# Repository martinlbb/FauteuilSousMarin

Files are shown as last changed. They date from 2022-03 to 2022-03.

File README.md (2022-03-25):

# FauteuilSousMarin

## Le projet 

Projet de Fauteuil sousmarin pour [Odysseus 3.1](https://odysseus31.com/ "Odysseus 3.1"), association à Lyon.

L'idée est de répliquer les mouvements du fauteuil spatial de la NASA dans les années 1980 sous l'eau.

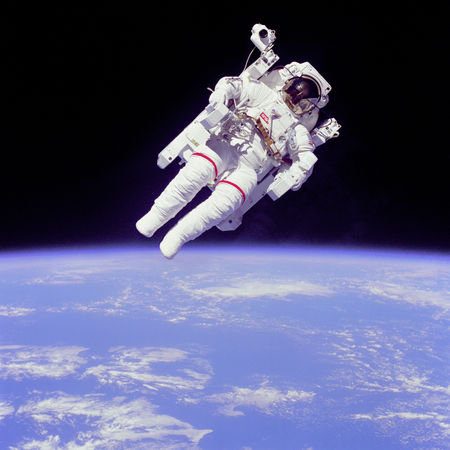
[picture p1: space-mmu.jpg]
<br><br>

Sous l'eau, pas de gravité, donc il est possible de simuler le fonctionnement d'un fauteuil spatial, pour se déplacer comme dans l'espace.

### Pour qui ?

* Pour les spationautes en formations (entrainement)
* Pour des personnes handicapées, qui seront prise en charge dans leurs déplacement sous l'eau.

## Principe du projet

Un fauteuil (cadre en tube soudé) acceuille le plongeur, son bloc d'air, deux joysticks, les moteurs et les batteries.

Le système est controllé par deux joysticks, inspirés directement des commandes de la NASA.
Une commande permet la translation du fauteuil sur les 3 axes (main gauche).
Une commande permet la rotation du fauteuil sur les 3 axes (main droite).
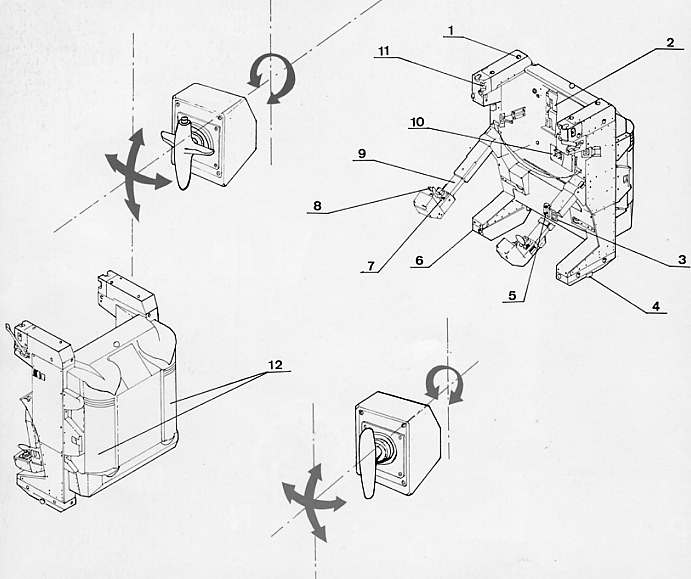
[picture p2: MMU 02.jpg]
<br><br>

Une commande à distance (Monitor box) permet le contrôle du fauteuil à distance, en parallèle ou en remplacement des commandes sur le fauteuil. Cette commande permet aussi d'armer le fauteuil lors de la mise à l'eau, pour éviter des salades de doigts (ou cheveux, ceinture de plomb, ...) avec les propulseurs.

Le fauteuil selon deux modes :
* plongée (normal) : quand l'ordre (joystick) s'arrête, l'action correspondante s'arrête
* espace (space) : quand l'ordre (joystick) s'arrête, l'action continue, comme dans l'espace. Le système est a améliorer, pour être plus réaliste. 

**DANGER**
Le surnom du mode 'espace' c'est 'Vicieux', vu les marches avant plein gaz (malgré l'arrêt de la commande) dans les murs de la piscine qui a servi aux tests. Bah oui, dans l'espace, quand tu as mis gaz avant toutes, il te faut gaz arrière toute pour compenser la première commande....

## Electronique

Un microcontrolleur Arduino gère le 'SpaceChair', en utilisant les entrées des joysticks et en dirigeant les propulseurs. Un mode 'SpaceMode' permet de simuler

Il contrôle ensuite 6 ESC (contrôlleur de moteur brushless (triphasé)) comme en modélisme.
Il y a 6 moteurs, 3 par axes et 2 par sens (avant/arrière). Je l'ai conçu pour équilibrer l'effet gyroscopique (moteur sens horaire et contra sens horaire sur chaque axe) et permettre plus de finesse.

## Impression 3D

De nombreux éléments du fauteuil ont été désignés sous openSCAD. Boitier de commande, protection des joysticks sous l'eau, chapeau des joysticks avec la réplique des commandes NASA.

## Annexes

### Le fauteuil MMU

Nasa: Manned Maneuvering Unit ou MMU, utilisé en 1984 !
Retiré car trop dangereux (24,4m/s de vitesse, donc en cas d'erreur, c'est bye bye la station et bonjour l'effet **vers l'infini et au delà**).
Depuis, passage au Simplified Aid for EVA Rescue : SAFER.
Il fait un delta de 3,3 m/s

MMU: 24 petites tuyères, chacune pouvant créer une poussée de 7,5 kg
3-axes Translatio controlleur (main gauche)
3-axes Rotation controlleur (main gauche)
Commandes simple ou mutli-axes en continues ou impulsions.

Son mode d'emploi : http://large.stanford.edu/courses/2014/ph240/clark1/docs/mcr-78-617.pdf

Un site qui en parle : http://capcomespace.net/dossiers/espace_US/shuttle/sts/EMU_MMU/MMU.htm

### Liste des composants
Voir aussi dans le dossier Datasheets !

* 6 moteurs, en 3 lots de CW et CWW https://www.aliexpress.com/item/32965239368.html
* 6 controlleurs 90A étanche : https://hobbyking.com/fr_fr/hobbyking-90a-boat-esc-4a-sbec.html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
* 1 télécommande de programmation : https://hobbyking.com/fr_fr/hobbyking-boat-esc-programming-card.html
* 4 joysticks 3 axes :  JH-D300X-R4 https://www.aliexpress.com/item/32992844960.html
* 6 potentiometres IP68 Vishay P13SM : https://www.vishay.com/docs/51064/p13sm.pdf
* 2 Arduino Micro

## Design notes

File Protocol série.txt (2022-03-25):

$G:

Start sequence=$
End sequence  =!

Commandes:
G pour commande joystick
	G:translateX%:translateY%:translateZ%:rotateX%:rotateY%:rotateZ%!
H pour commande joystick qui prends la main
	G:translateX%:translateY%:translateZ%:rotateX%:rotateY%:rotateZ%!
M pour Mode
	M:mode!
	parameters
		SPACE as S, SpaceMode
		DIVE as D,  DiveMode
		ARMED as A
		DISARMED as X
D pour Debug
	$D!
	S'inverse tout seul à chaque ordre
S pour Save
	$S!
	Sauve les paramètres dans l'eeprom interne
P pour parameter
	P:parametername:value:value!
	parameters
		INVERSE as I, Translate(T) or Rotate (R), which axis (X,Y or Z), inverse it(1) or not (0). $P:I:T:X:1!
		NEUTRAL as N, percentage value. $P:N:8!
		THRUSTER as T, Forward(F) or Reverse (R), which axis (X,Y or Z), max running %. $P:T:R:Z:70!
		KINETIC as K, percentage of ignored kinetc value. $P:K:10!

$P:I:T:Z:1!

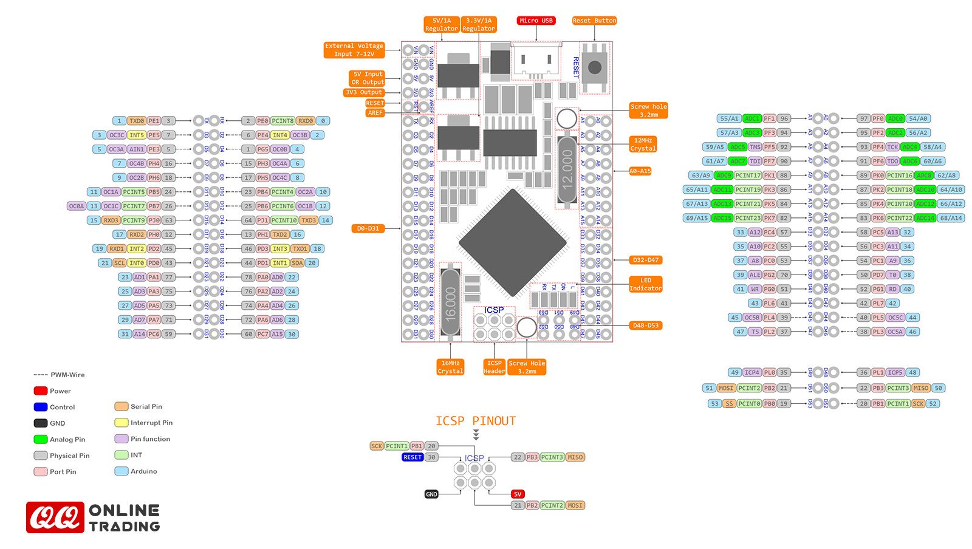
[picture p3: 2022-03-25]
datasheets/mega 2560 pro embed pinout.jpg

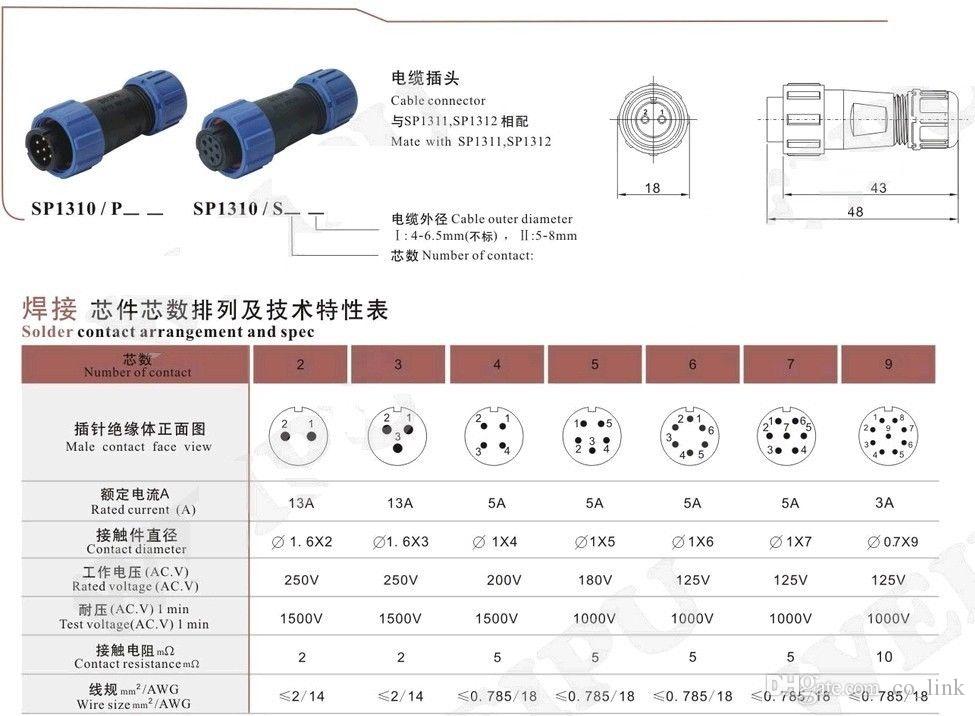
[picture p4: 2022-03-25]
datasheets/IP68-SP13-elec.jpg

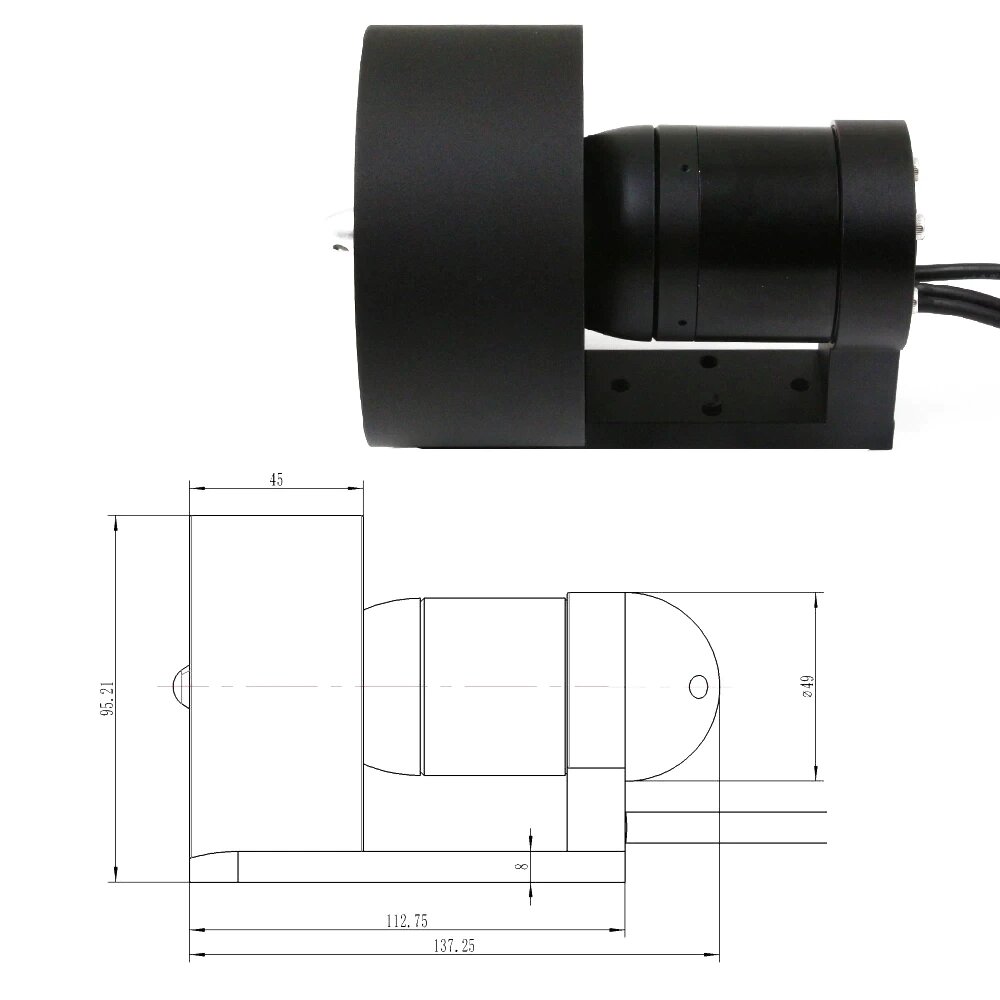
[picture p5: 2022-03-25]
datasheets/DS-02Thruster Profil.jpg

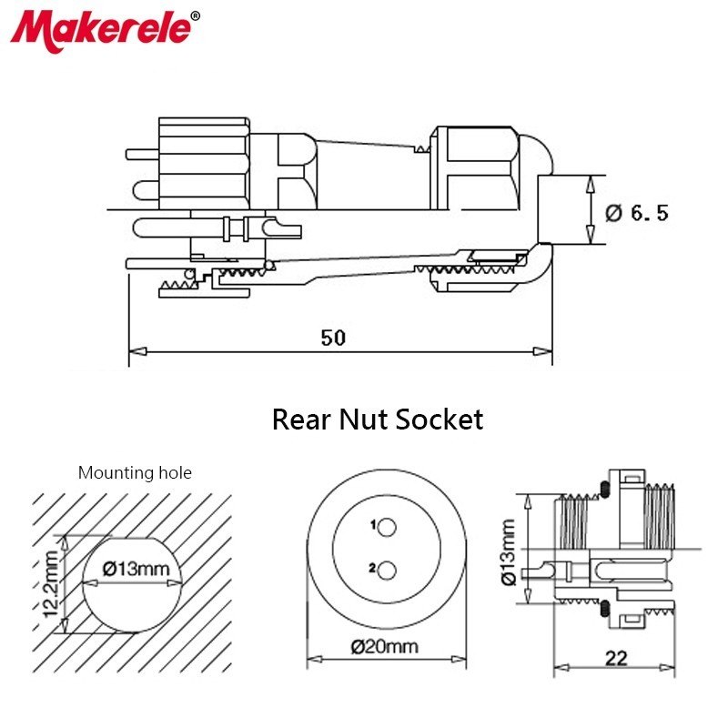
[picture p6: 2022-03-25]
datasheets/IP68-SP13.jpg

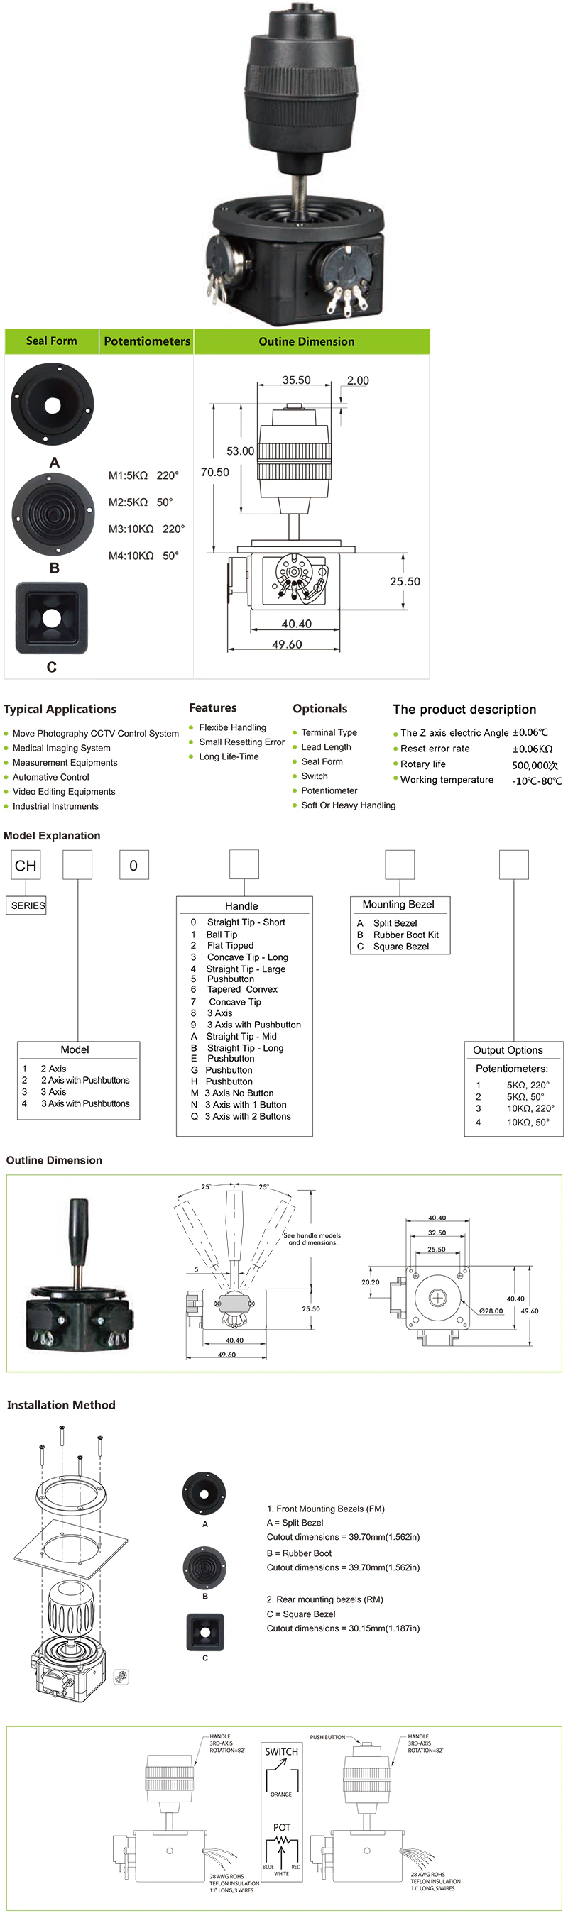
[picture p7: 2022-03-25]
datasheets/joystick-3axis.jpg

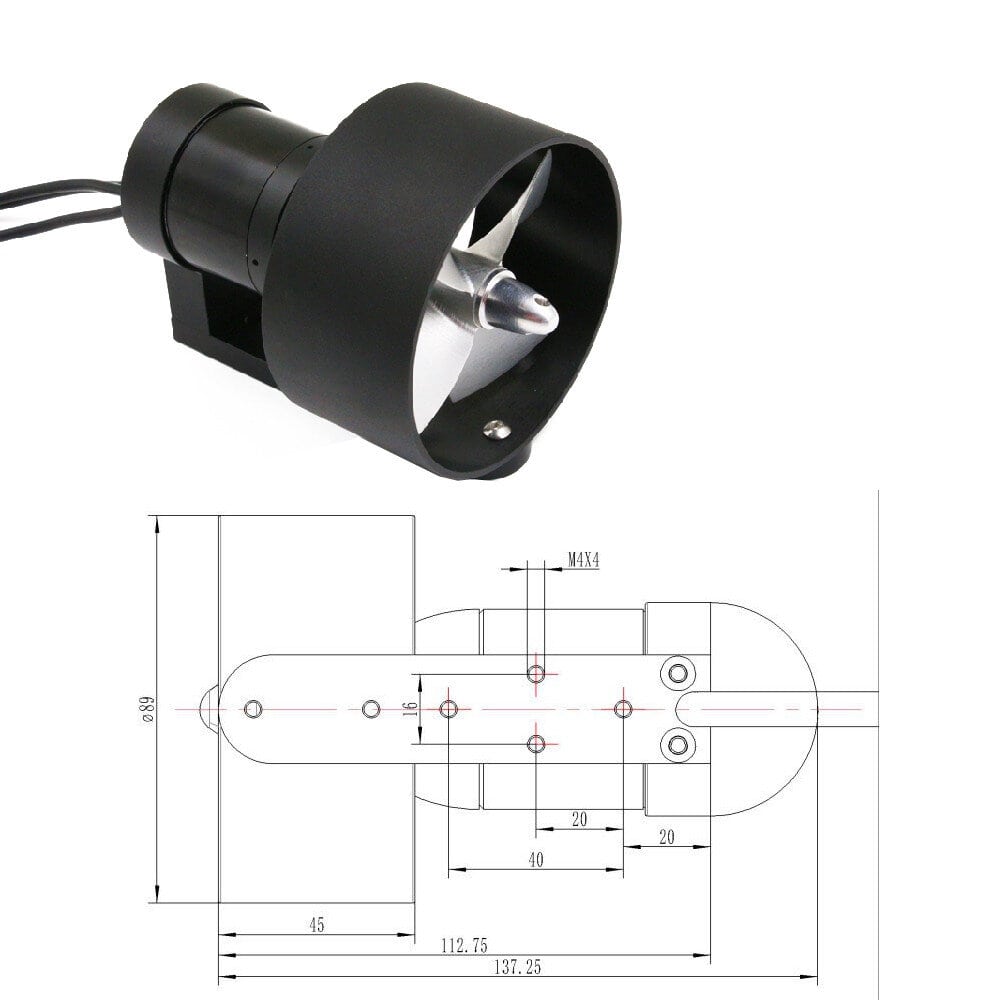
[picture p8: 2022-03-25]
datasheets/DS-02 Thruster fond_.jpg

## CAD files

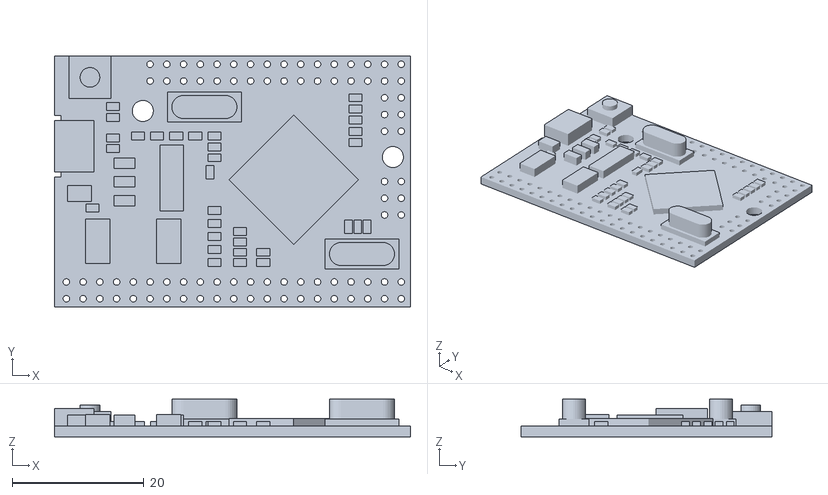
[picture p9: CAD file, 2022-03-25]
Monitor box/Box 3D/Mega_2560_PRO_Embed_CH340G.stl
54.0 x 38.0 x 5.70

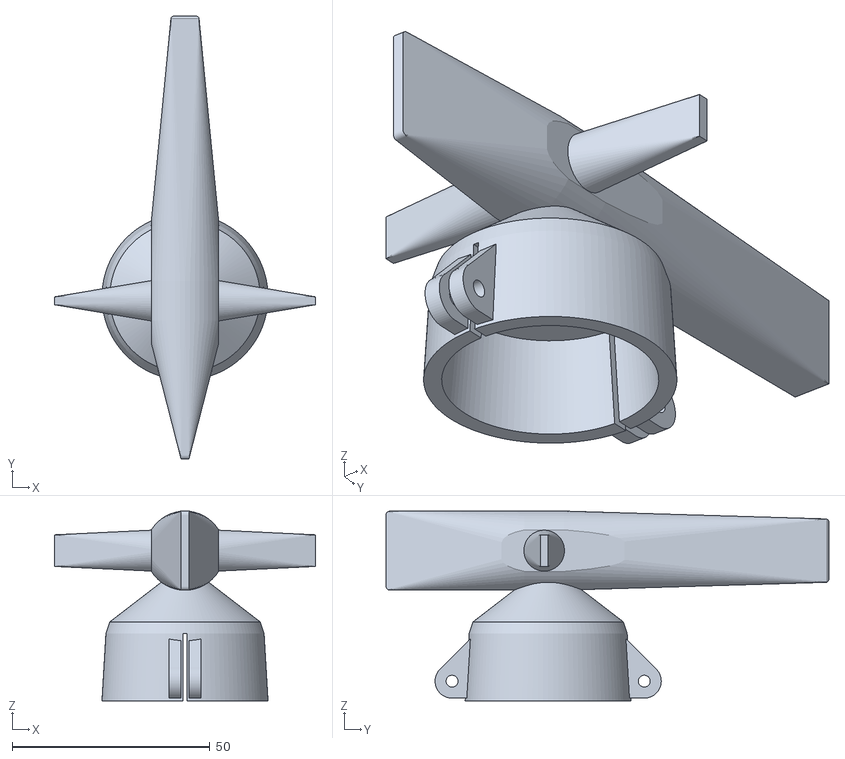
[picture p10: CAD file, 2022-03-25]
SpaceChair/joystick_rotate.stl
66.0 x 112.0 x 48.0

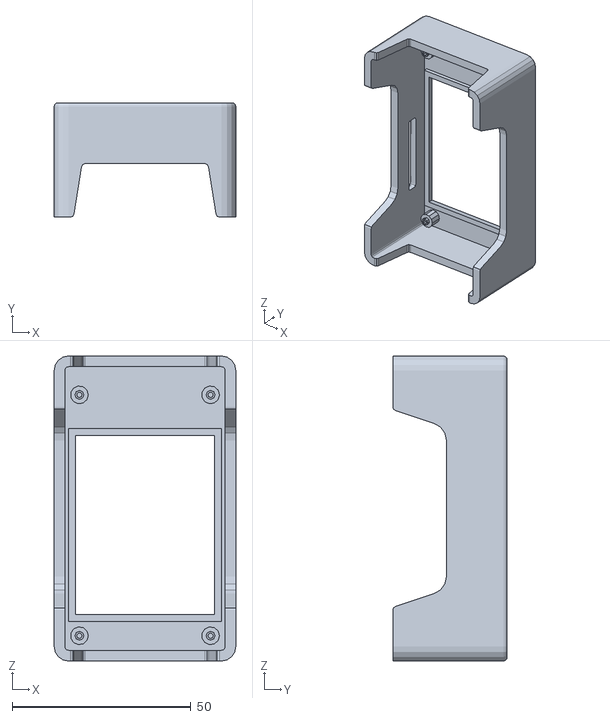
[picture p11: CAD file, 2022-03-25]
Monitor box/Box 3D/TFT_housing.stl
50.8 x 32.0 x 85.3

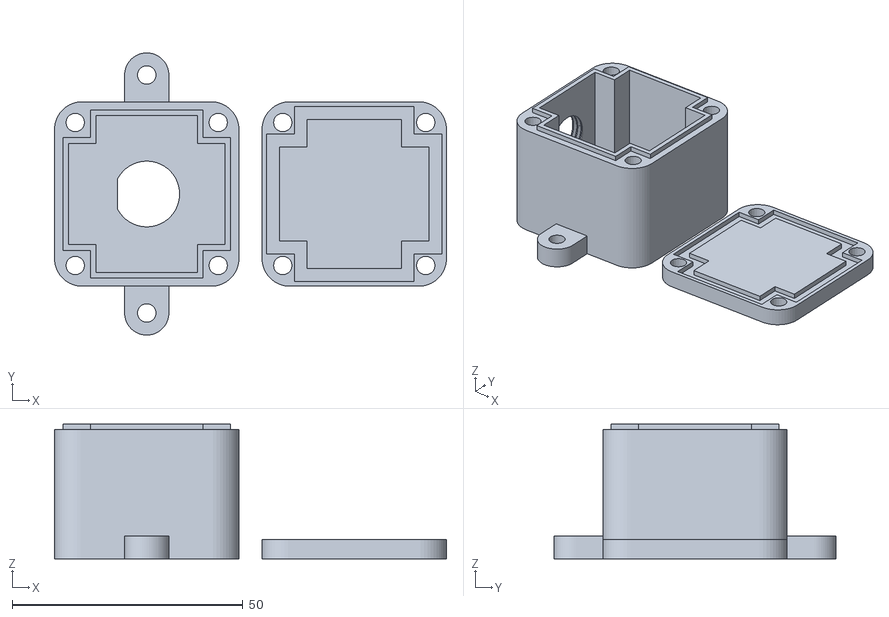
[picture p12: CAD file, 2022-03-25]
SpaceChair/box_surface_link.stl
85.0 x 61.2 x 29.2

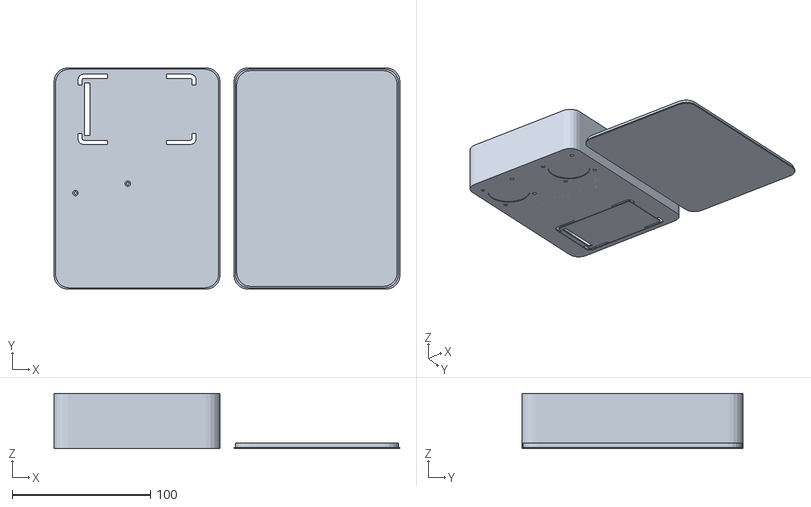
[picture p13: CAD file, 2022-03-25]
Monitor box/Box 3D/monitor_box.stl
250.0 x 160.0 x 40.0

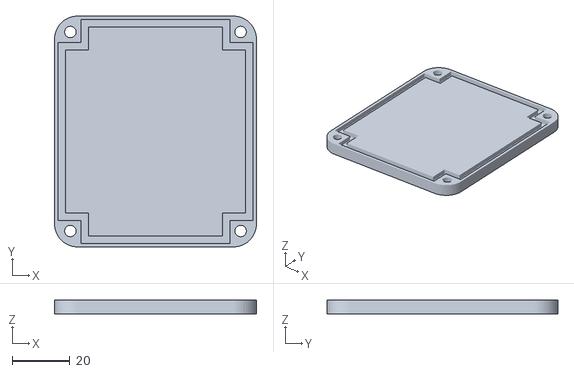
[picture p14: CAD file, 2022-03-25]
SpaceChair/box_joystick_V2_lid.stl
70.0 x 80.0 x 5.00

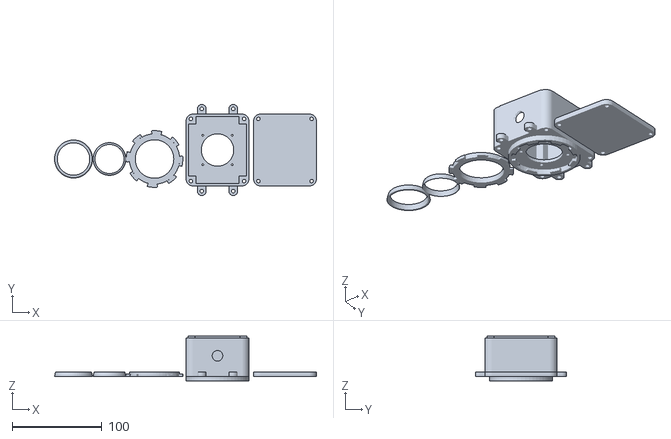
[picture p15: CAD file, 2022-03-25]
SpaceChair/box_joystick_V2.stl
291.1 x 101.2 x 50.0

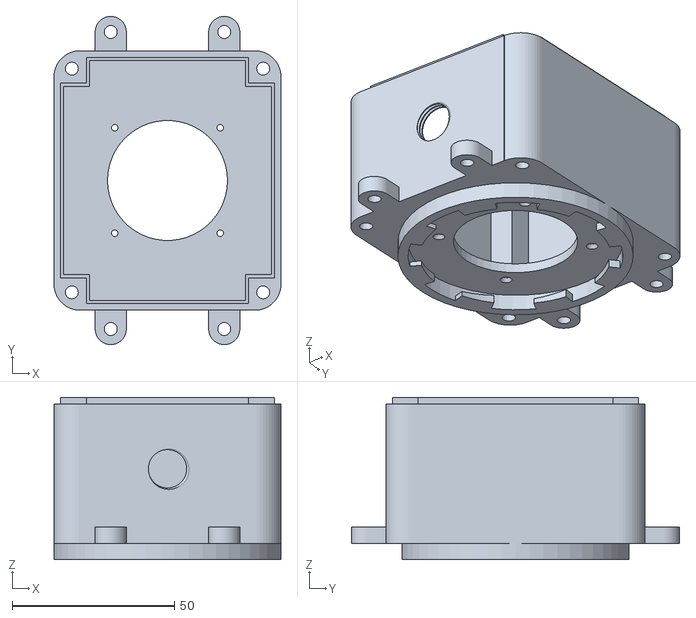
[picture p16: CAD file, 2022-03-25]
SpaceChair/box_joystick_V2_case.stl
70.0 x 101.2 x 50.0

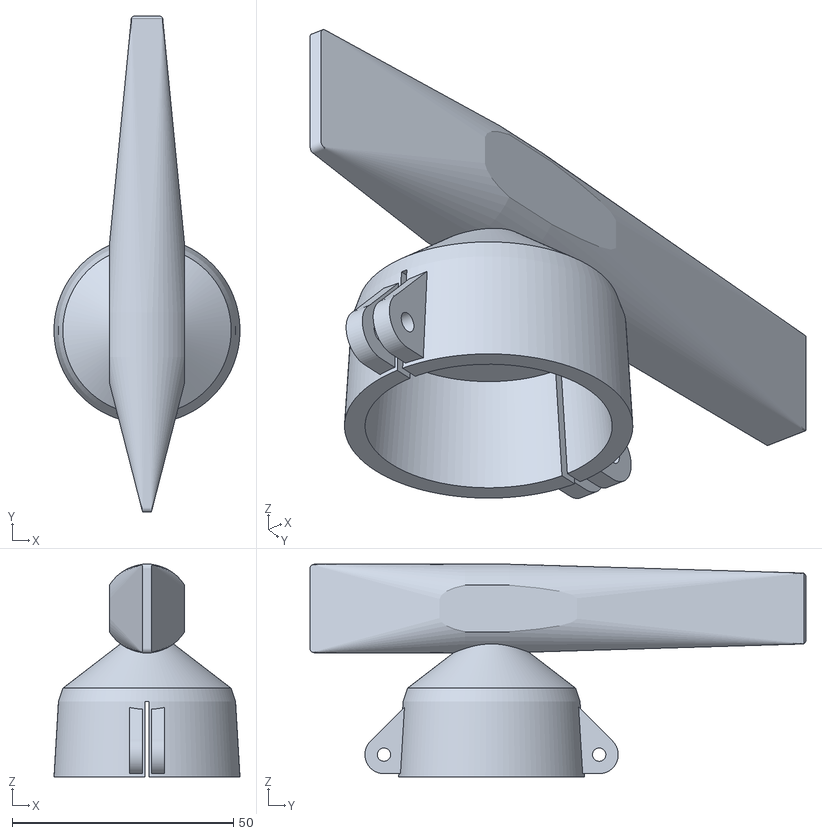
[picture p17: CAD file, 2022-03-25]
SpaceChair/joystick_translate.stl
42.0 x 112.0 x 48.0

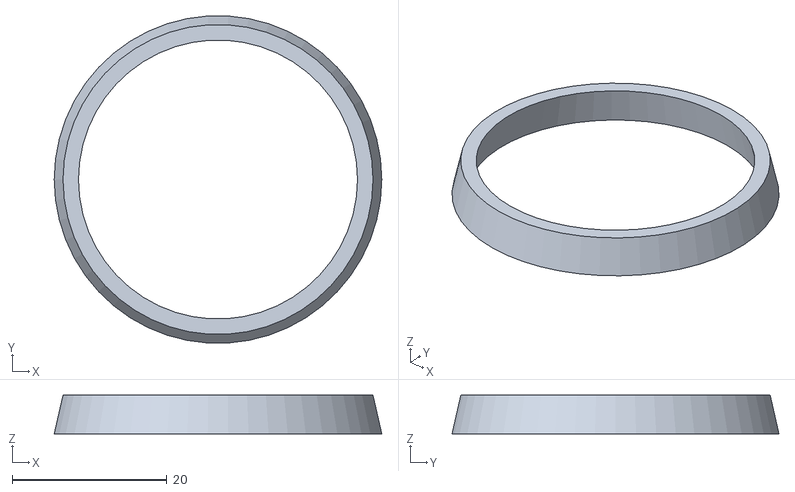
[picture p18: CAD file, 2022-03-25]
SpaceChair/box_joystick_V2_middle_ring.stl
42.3 x 42.2 x 5.00

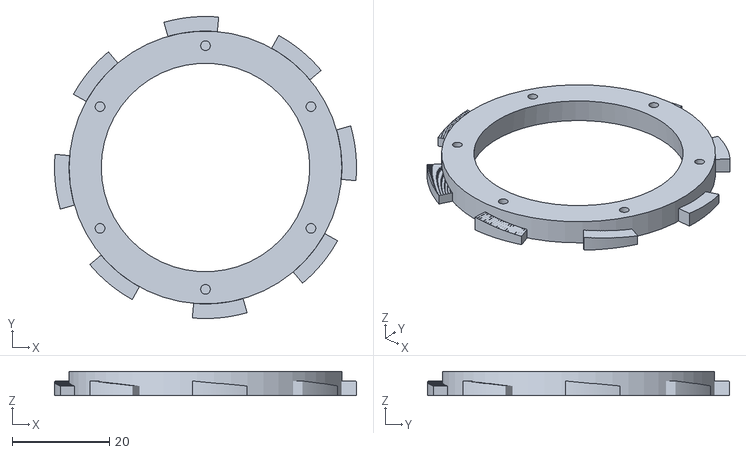
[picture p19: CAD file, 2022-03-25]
SpaceChair/box_joystick_V2_outter_ring.stl
62.0 x 62.0 x 5.00

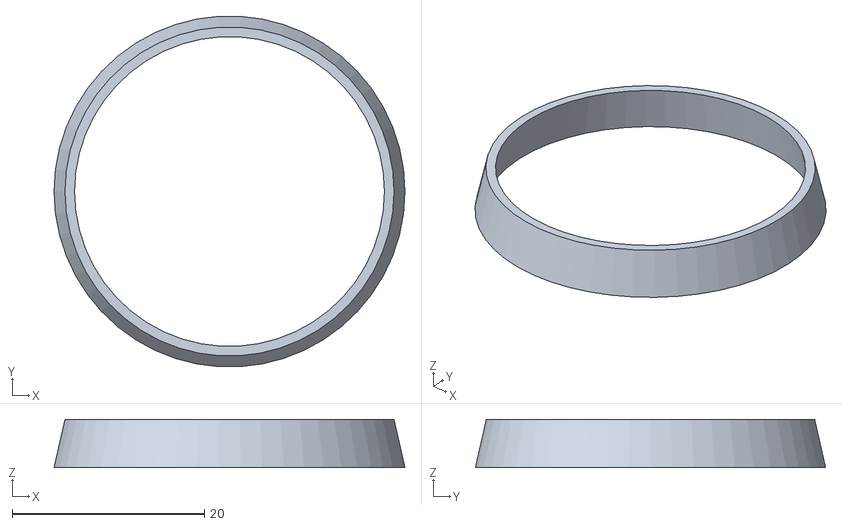
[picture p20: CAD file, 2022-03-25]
SpaceChair/box_joystick_V2_inner_ring.stl
36.5 x 36.4 x 5.00

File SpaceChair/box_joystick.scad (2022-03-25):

/* [Box Options] */
// Dimension: Box outer X-Size [mm]
box_Size_X          = 70;
// Dimension: Box outer Y-Size [mm]
box_Size_Y          = 70;
// Dimension: Box Inner height [mm]
box_Inner_Height    = 40;
// Box bottom/top thickness
box_BottomTop_Thickness =  3; // [0.6:0.2:3]
// Edge corner radius 
box_Screw_Corner_Radius   =  6; // [2:1:10]
// four outer screw hole diameters
box_Screw_Diameter     =  3.2; // [2:0.2:4]
// Box wall thickness
box_Wall_Thickness     =  3.6; // [0.4:0.2:3.2]
/* [Top Barrier Options] */
// Box barrier thickness
barrier_Thickness  =  1.2; // [0.4:0.2:3.2]
// Box barrier height
barrier_Height     =  2;   // [1.0:0.2:8]
// Additional width on the lid to correct for badly calibrated printers
barrier_Tolerance  =  0.8; // [0.0:0.1:1]
/* [Mouting Screw Nose Options] */
// Number of screw noses
screwnose_Number        = 4; // [0:No noses, 2: one top/one bottom, 4: two top/two bottom]
// Diameter of the noses' screw holes
screwnose_Diameter      = 4; // [2:0.2:8]
// Height of the noses
screwnose_Height        = 5; // [2:0.2:10]
// Wall thickness
screwnose_Wall_Thickness = 2.8; // [2:0.2:5]
//joystick screws
joystick_Screw = 2;  //usually 2mm
joystick_Screw_CS = 3.5; //countersink area for screw
joystick_Screw_CS_H = 1.2; //countersitck depth
joystick_Holes_X = 32.5; //32.5 for FTF-D300 joystick
joystick_Holes_Y = 32.5; //32.5 for FTF-D300 joystick

// **************************
// ** Calculated globals
// **************************
boxHeight = box_Inner_Height+box_BottomTop_Thickness;
include <threads.scad>;

module box() {
	barrier_Thickness = box_Wall_Thickness-barrier_Thickness;
	difference() {
		union() {
			// solid round box, corners
			translate([box_Screw_Corner_Radius, box_Screw_Corner_Radius, 0]) cylinder(r=box_Screw_Corner_Radius, h=boxHeight, $fn=50); // bottom left
			translate([box_Size_X-box_Screw_Corner_Radius, box_Screw_Corner_Radius, 0]) cylinder(r=box_Screw_Corner_Radius, h=boxHeight, $fn=50); // bottom right
			translate([box_Screw_Corner_Radius, box_Size_Y-box_Screw_Corner_Radius, 0]) cylinder(r=box_Screw_Corner_Radius, h=boxHeight, $fn=50); // top left
			translate([box_Size_X-box_Screw_Corner_Radius, box_Size_Y-box_Screw_Corner_Radius, 0]) cylinder(r=box_Screw_Corner_Radius, h=boxHeight, $fn=50); // bottom right
			// solid round box, inner filling
			translate([0, box_Screw_Corner_Radius, 0]) cube([box_Size_X, box_Size_Y-2*box_Screw_Corner_Radius, boxHeight]);
			translate([box_Screw_Corner_Radius, 0, 0]) cube([box_Size_X-2*box_Screw_Corner_Radius, box_Size_Y, boxHeight]);
			// solid round box, top border
			translate([barrier_Thickness, box_Screw_Corner_Radius+barrier_Thickness, 0]) cube([box_Size_X-2*barrier_Thickness, box_Size_Y-2*box_Screw_Corner_Radius-2*barrier_Thickness, boxHeight+barrier_Height]);
			translate([box_Screw_Corner_Radius+barrier_Thickness, barrier_Thickness, 0]) cube([box_Size_X-2*box_Screw_Corner_Radius-2*barrier_Thickness, box_Size_Y-2*barrier_Thickness, boxHeight+barrier_Height]);
		}
		// inner cut-out
		translate([box_Wall_Thickness, box_Screw_Corner_Radius+box_Wall_Thickness, box_BottomTop_Thickness]) cube([box_Size_X-2*box_Wall_Thickness, box_Size_Y-2*box_Screw_Corner_Radius-2*box_Wall_Thickness, boxHeight+barrier_Height]);
		translate([box_Screw_Corner_Radius+box_Wall_Thickness, box_Wall_Thickness, box_BottomTop_Thickness]) cube([box_Size_X-2*box_Screw_Corner_Radius-2*box_Wall_Thickness, box_Size_Y-2*box_Wall_Thickness, boxHeight+barrier_Height]);
		// Screw holes
		translate([(box_Screw_Corner_Radius+box_Wall_Thickness)/2,(box_Screw_Corner_Radius+box_Wall_Thickness)/2,0]) cylinder(r=box_Screw_Diameter/2, h=boxHeight, $fn=20);
		translate([(box_Screw_Corner_Radius+box_Wall_Thickness)/2,box_Size_Y-(box_Screw_Corner_Radius+box_Wall_Thickness)/2,0]) cylinder(r=box_Screw_Diameter/2, h=boxHeight, $fn=20);
		translate([box_Size_X-(box_Screw_Corner_Radius+box_Wall_Thickness)/2,(box_Screw_Corner_Radius+box_Wall_Thickness)/2,0]) cylinder(r=box_Screw_Diameter/2, h=boxHeight, $fn=20);
		translate([box_Size_X-(box_Screw_Corner_Radius+box_Wall_Thickness)/2,box_Size_Y-(box_Screw_Corner_Radius+box_Wall_Thickness)/2,0]) cylinder(r=box_Screw_Diameter/2, h=boxHeight, $fn=20);
        //Screws for joystick
        translate([(box_Size_X/2)+(joystick_Holes_X/2),(box_Size_Y/2)+(joystick_Holes_Y/2),0]) cylinder(r=joystick_Screw/2, h=boxHeight, $fn=40);
        translate([(box_Size_X/2)+(joystick_Holes_X/2),(box_Size_Y/2)-(joystick_Holes_Y/2),0]) cylinder(r=joystick_Screw/2, h=boxHeight, $fn=40);
        translate([(box_Size_X/2)-(joystick_Holes_X/2),(box_Size_Y/2)+(joystick_Holes_Y/2),0]) cylinder(r=joystick_Screw/2, h=boxHeight, $fn=40);
        translate([(box_Size_X/2)-(joystick_Holes_X/2),(box_Size_Y/2)-(joystick_Holes_Y/2),0]) cylinder(r=joystick_Screw/2, h=boxHeight, $fn=40);
        //Countersink for joystick screws
        translate([(box_Size_X/2)+(joystick_Holes_X/2),(box_Size_Y/2)+(joystick_Holes_Y/2),0]) rotate_extrude($fn=40) polygon( points=[[0,0],[joystick_Screw_CS/2,0],[1,joystick_Screw_CS_H],[0,joystick_Screw_CS_H]] );
        translate([(box_Size_X/2)+(joystick_Holes_X/2),(box_Size_Y/2)-(joystick_Holes_Y/2),0]) rotate_extrude($fn=40) polygon( points=[[0,0],[joystick_Screw_CS/2,0],[1,joystick_Screw_CS_H],[0,joystick_Screw_CS_H]] );
        translate([(box_Size_X/2)-(joystick_Holes_X/2),(box_Size_Y/2)+(joystick_Holes_Y/2),0]) rotate_extrude($fn=40) polygon( points=[[0,0],[joystick_Screw_CS/2,0],[1,joystick_Screw_CS_H],[0,joystick_Screw_CS_H]] );
        translate([(box_Size_X/2)-(joystick_Holes_X/2),(box_Size_Y/2)-(joystick_Holes_Y/2),0]) rotate_extrude($fn=40) polygon( points=[[0,0],[joystick_Screw_CS/2,0],[1,joystick_Screw_CS_H],[0,joystick_Screw_CS_H]] );
        
        //Opening hole for joystick
        translate([box_Size_X/2, box_Size_Y/2, 0]) cylinder(r=14, h=boxHeight, $fn=50);
		//Adding PG-7 thread for cable gland
        //Usual diameter is 12.5. Need to use 13.2 to allow smooth tightening
		translate([box_Size_X/2,(box_Wall_Thickness+0.1), box_Wall_Thickness+((boxHeight-box_Wall_Thickness)/2)]) rotate([90,00,0]) difference () {metric_thread (diameter=13.2, pitch=1.27, length=4, internal=true);};
    }
    //Waterproof inner ring
    translate([box_Size_X/2, box_Size_Y/2, 0]) rotate_extrude($fn=50) polygon( points=[[14,0],[14,-5.5],[17,-5.5],[19,0]] );
    //Waterproof outter ring
    translate([box_Size_X/2, box_Size_Y/2, -5.5]) difference () {
    cylinder(r=31, h=5.5, $fn=50);
    metric_thread (diameter=50, pitch=1.4, length=5.5, internal=true);
    };
    
	// Lower nose(s)
	if (screwnose_Number==2) translate([box_Size_X/2, 0.001, 0]) mirror([0,1,0]) screwNose(screwnose_Diameter, screwnose_Height);
	if (screwnose_Number==4) {
		translate([box_Size_X*0.25, 0.001, 0]) mirror([0,1,0]) screwNose(screwnose_Diameter, screwnose_Height);
		translate([box_Size_X*0.75, 0.001, 0]) mirror([0,1,0]) screwNose(screwnose_Diameter, screwnose_Height);
	}
	// Upper nose(s)
	if (screwnose_Number==2) translate([box_Size_X/2, box_Size_Y-0.001, 0]) screwNose(screwnose_Diameter, screwnose_Height);
	if (screwnose_Number==4) {
		translate([box_Size_X*0.25, box_Size_Y-0.001, 0]) screwNose(screwnose_Diameter, screwnose_Height);
		translate([box_Size_X*0.75, box_Size_Y-0.001, 0]) screwNose(screwnose_Diameter, screwnose_Height);
	}
}
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

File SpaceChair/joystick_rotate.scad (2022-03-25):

screwnose_Diameter      = 4; // [2:0.2:8]
// Height of the noses
screwnose_Height        = 5; // [2:0.2:10]
// Wall thickness
screwnose_Wall_Thickness = 2.8; // [2:0.2:5]
box_Screw_Corner_Radius   =  6; // [2:1:10]
// four outer screw hole diameters
box_Screw_Diameter     =  3.2; // [2:0.2:4]

module pinch(h=1,r1=1,r2=1,r3=0) {
    zero = 0.00000000001;
    steps = $fn ? $fn : $fa;
    res = h/steps;
    r1 = r1 ? r1 : res;
    r2 = r2 ? r2 : res;
    r3 = r3 ? r3 : zero;
    hull() {
        cylinder(h=zero,r=r1,r2=res,r3=0,center=false);
        translate([-r2, -r3, h - zero]) cube([
            r2 * 2,
            r3 * 2,
            zero
        ]);
    }
}


//Caps to fit on top of joystick
difference (){
rotate_extrude($fn=100) polygon( points=[[18,0],[21,0],[20,17],[19,20],[0,20],[0,17],[16.5,17]] );
translate ([0,0,8.5]) rotate([0,90,0]) cube([17,42,1],true);
};
translate ([0,0,20]) cylinder(h=10, r1=19, r2=6, center=false, $fn=100);
//Hearings caps
translate([1, 19, 5]) rotate([0,90,0]) screwNose(3, 3);
translate([-4, 19, 5]) rotate([0,90,0]) screwNose(3, 3);    
translate([-1, -19, 5]) rotate([180,90,0]) screwNose(3, 3);    
translate([4, -19, 5]) rotate([180,90,0]) screwNose(3, 3); 
translate ([1,18,11]) rotate([-45,0,0]) cube([3,5,3]);
translate ([1,17.9,14]) rotate([-45,0,0]) cube([3,11,2.5]);

translate ([-4,18,11]) rotate([-45,0,0]) cube([3,5,3]);
translate ([-4,17.9,14]) rotate([-45,0,0]) cube([3,11,2.5]);
translate ([1,-22,7.5]) rotate([45,0,0]) cube([3,5,3]);
translate ([1,-25.1,6.7]) rotate([45,0,0]) cube([3,11,2.5]);

translate ([-4,-22,7.5]) rotate([45,0,0]) cube([3,5,3]);
translate ([-4,-25.1,6.7]) rotate([45,0,0]) cube([3,11,2.5]);



//Handle in + shape (rotation)
translate([0, 9, 38]) rotate([0,0,90]) union () {difference () {
union () {
translate([-10,0,0]) rotate([0,-90,0]) cylinder(10,10, 10, center=true, $fn=50);
translate([-15,0,0]) rotate([0,-90,0]) pinch(35, 10, 10, 1, $fn=50);
translate([-5,0,0]) rotate([180,-90,0]) pinch(67, 10, 8, 3.5, $fn=50);
//
};
//Edges
translate ([61,2.7,-9]) difference() { cube([2,2,18]); cylinder(18, 1, 1,  $fn=50);};
translate ([61,-2.7,-9]) rotate ([0,0,-90]) difference() { cube([2,2,18]); cylinder(18, 1, 1,  $fn=50);};
translate ([61,8,7.1]) rotate ([90,0,0]) difference() { cube([2,2,18]); cylinder(18, 1, 1,  $fn=50);};
translate ([61,-8,-7.1]) rotate ([-90,0,0]) difference() { cube([2,2,18]); cylinder(18, 1, 1,  $fn=50);};
translate ([-49,0.8,-10]) rotate ([0,0,90]) difference() { cube([2,2,22]); cylinder(22, 1, 1,  $fn=50);};
translate ([-49,-0.8,-10]) rotate ([0,0,180]) difference() { cube([2,2,22]); cylinder(22, 1, 1,  $fn=50);};
translate ([-49,8,9]) rotate ([90,-90,0]) difference() { cube([2,2,18]); cylinder(18, 1, 1,  $fn=50);};
translate ([-49,-8,-9]) rotate ([-90,90,0]) difference() { cube([2,2,18]); cylinder(18, 1, 1,  $fn=50);};
//Sides
translate ([0,11,0]) cube([80, 5, 32], center=true);
translate ([0,-11,0]) cube([80, 5, 32], center=true);
};
translate ([-10,-8,0]) rotate([90,90,0]) pinch(25, 5.2, 4, 1, $fn=50);
translate ([-10,8,0]) rotate([-90,90,0]) pinch(25, 5.2, 4, 1, $fn=50);
};

translate ([1,-22,7.5]) rotate([45,0,0]) cube([3,5,3]);
translate ([1,-25.1,6.7]) rotate([45,0,0]) cube([3,11,2.5]);

translate ([-4,-22,7.5]) rotate([45,0,0]) cube([3,5,3]);
translate ([-4,-25.1,6.7]) rotate([45,0,0]) cube([3,11,2.5]);






    module screwNose(screwholeDiameter=4, noseHeight=5) {
	additionalDistanceFromWall = 1;
	translate([0,screwholeDiameter/2+screwnose_Wall_Thickness+additionalDistanceFromWall, 0]) difference() {
		union() {
			translate([-(screwholeDiameter/2+screwnose_Wall_Thickness), -(screwholeDiameter/2+screwnose_Wall_Thickness+additionalDistanceFromWall),0]) cube([(screwholeDiameter/2+screwnose_Wall_Thickness)*2, screwholeDiameter/2+screwnose_Wall_Thickness+additionalDistanceFromWall, noseHeight]);
			cylinder(r=(screwholeDiameter/2)+screwnose_Wall_Thickness, h=noseHeight, $fn=60);
		}
		cylinder(r=screwholeDiameter/2, h=noseHeight, $fn=60);
	}
}

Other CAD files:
SpaceChair/box_joystick_V2.scad
SpaceChair/box_surface_link.scad
Monitor box/Box 3D/monitor_box.scad
SpaceChair/joystick_translate.scad

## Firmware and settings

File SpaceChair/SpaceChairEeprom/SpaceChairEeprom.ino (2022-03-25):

/*
 * Fauteuil Spatial 
 * 
 * Odysseus 3.1
 */

#include <Servo.h>
#include <EEPROM.h>


//Variable declaration
//Two 3 axis joysticks are available.
//'|' axis is translation (left hand)
//'+' axis is rotation (right hand)
#define translateXpin A1
#define translateYpin A3
#define translateZpin A5
#define rotateXpin A0
#define rotateYpin A2
#define rotateZpin A4

//ESC location
#define xCWPin  2
#define xCCWPin 3
#define yCWPin  4
#define yCCWPin 5
#define zCWPin  6
#define zCCWPin 7

//MAX485 location
//RE is 22 GND
//DE is 23 GND
#define RE 22
#define DE 23

struct parameters {
  unsigned long magic=false;
  byte struct_version;
  //Enable to inverse (swap) current axis value
  bool inverseTranslateX;
  bool inverseTranslateY;
  bool inverseTranslateZ;
  bool inverseRotateX;
  bool inverseRotateY;
  bool inverseRotateZ;
  //Neutral ignore
  //Define how much percentage must be ignored
  //around neutral
  //Axis value is usually -100%<->0%<->+100%
  //Then everyting arrounf -neutral%<->0%<->+neutral%
  //will be ignored. Default is 8%
  //Value must be between 0 and 20 maximum.
  int neutralPercent;
  //Space mode selector
  bool spaceMode;
  //Neutral limit to avoid boucing
  //usually 10%
  int  kineticNeutralLevel;
  //Kinetic limit
  //Usually defined at 1000 (100% * 10)
  int kineticMaxLevel;
  //Thuster max power
  //define max percentage of power
  //this thruster can handle (usually
  // up to 100%)
  //Allow limiting Forward power to
  //compensate for Reverse power
  //ie: FW=70%, RV=100%
  int thrusterXForwardMax;
  int thrusterXReverseMax;
  int thrusterYForwardMax;
  int thrusterYReverseMax;
  int thrusterZForwardMax;
  int thrusterZReverseMax;
  //Debug flag for output on USB/serial
  bool debug;
};

/*
 * system values
 * Do NOT modify
 */ 
//Axis raw values
int translateX = 0;
int translateY = 0;
int translateZ = 0;
int rotateX = 0;
int rotateY = 0;
int rotateZ = 0;


//JoystickPercent
//Per joystick current position
//in percent (-100%<->0%<->+100%
struct joystickPercent {
  int X = 0;
  int Y = 0;
  int Z = 0;
};

//Thruster percentage
//Per axis thrust level in percent
struct thrustLevel {
    //thrust for clockwise (CW) motor
    int CW = 0;
    //thrust for counter clockwise (CCW) motor
    int CCW = 0;
    //Kinetic value for space mode
    int kineticCW = 0;
    int kineticCCW = 0;
};

//Magic number for Eeprom
static const unsigned long STRUCT_MAGIC = 78851203;
static const byte STRUCT_VERSION = 1;

//To deal with serial orders
const byte numChars = 32;
char receivedChars[numChars];
char tempChars[numChars];        // temporary array for use when parsing
boolean newData = false;

//Global wide variable with parameters

bool armed = false;
parameters p;
//ESC declaration
Servo xCW, xCCW, yCW, yCCW, zCW, zCCW;


//Per axis definition 
struct thrustLevel thrustX;
struct thrustLevel thrustY;
struct thrustLevel thrustZ;

//Per joystick definition 
struct joystickPercent translation;
struct joystickPercent rotation;

void setup() {
  //Initialize MAS485
  pinMode(DE, OUTPUT);
  pinMode(RE, OUTPUT);
  digitalWrite(DE, LOW);
  digitalWrite(RE, LOW);
  
  
  //Initialize serial debug link
  Serial.begin(115200);
  while (!Serial) {
     ; // wait for serial port to connect. Needed for native USB
  }
  Serial.println("SpaceChair ready");
  //RS485 serial link 
  Serial1.begin(115200);

  //Load parameters
  loadEEPROM();

  //Initialize ESC
  xCW.attach(xCWPin,1000,2000); //X CW
  xCCW.attach(xCCWPin,1000,2000); //X CCW
  yCW.attach(yCWPin,1000,2000); //Y CW
  yCCW.attach(yCCWPin,1000,2000); //Y CCW
  zCW.attach(zCWPin,1000,2000); //Z CW
  zCCW.attach(zCCWPin,1000,2000); //Z CCW
  
}

//Convert current axis value to a real percent
int joystickToPercent (int analogValue, bool inversedAxis = false){

  int value = (100 - (constrain((analogValue),0,1000) / 5));

  //Neutral adjustement, to avoid motor spinning while joystick is around neutral position
  //will ignore some percentage (defined in neutralPercent)
  if ((value > -p.neutralPercent) && (value < p.neutralPercent) ) {
    value = 0;
  } else {
    //Recompute value to ignore neutral while driving motor smootlhy
    if ( value > 0){
      //For positive value
      value = (value * (1 + (p.neutralPercent * 0.01))) - p.neutralPercent;
    } else {
      value = (value * (1 + (p.neutralPercent * 0.01))) + p.neutralPercent;
    }
  }

  //Inverted Axis, inverse return value
  if (inversedAxis == true){
    value = value * -1;
  }

  return value;
}

//Convert joystick percentage value to real thrust order
struct thrustLevel percentToThrust (struct thrustLevel thrust, int translationAxisPercent, int rotationAxisPercent){
   //Translation thrust values
   int tCW, tCCW = 0;
   //Rotation thrust values
   int rCW, rCCW = 0;

   //Compute translation
   tCW = translationAxisPercent;
   tCCW = -translationAxisPercent;
   
   //Compute rotation
   rCW = rCCW = rotationAxisPercent;
  
   //Mix values
   //Do we are higher then max available thrust?
   if(abs(tCW)+abs(rCW) > 100){
     //lower proportionnaly max output value
     thrust.CW = (tCW+rCW)*(100.0 / (abs(tCW)+abs(rCW)));
     thrust.CCW = (tCCW+rCCW) * (100.0 / (abs(tCCW)+abs(rCCW)));
   } else {
    //We do not exceed max thrust
     thrust.CW = tCW+rCW;
     thrust.CCW = tCCW+rCCW;
   }

   return thrust;
}

//Create a fake spatial effect, when each order needs
//to be reciproced. In space we don't have water to slow us
struct thrustLevel spaceKineticThrust (struct thrustLevel spaceThrust){
 
   //Add kinetic energy
   spaceThrust.kineticCW = spaceThrust.kineticCW + spaceThrust.CW;
   spaceThrust.kineticCCW = spaceThrust.kineticCCW + spaceThrust.CCW;
   
   //We cap kinetic energy to a max (usually defined at 1000) on CW thuster
   if( (spaceThrust.kineticCW > 0 ) && (spaceThrust.kineticCW > p.kineticMaxLevel) ) {
    spaceThrust.kineticCW = p.kineticMaxLevel;
   } else if( (spaceThrust.kineticCW < 0) && (spaceThrust.kineticCW < -p.kineticMaxLevel) ) {
    spaceThrust.kineticCW = -p.kineticMaxLevel;
   }
   //Cap for neutral (easier stops)
   if( (spaceThrust.kineticCW > -p.kineticNeutralLevel) && (spaceThrust.kineticCW < p.kineticNeutralLevel) ) {
    spaceThrust.kineticCW = 0;
   }
   //For CCW
   if( (spaceThrust.kineticCCW > 0 ) && (spaceThrust.kineticCCW > p.kineticMaxLevel) ) {
    spaceThrust.kineticCCW = p.kineticMaxLevel;
   } else if( (spaceThrust.kineticCCW < 0) && (spaceThrust.kineticCCW < -p.kineticMaxLevel) ) {
    spaceThrust.kineticCCW = -p.kineticMaxLevel;
   }
   //Cap for neutral (easier stops)
   if( (spaceThrust.kineticCCW > -p.kineticNeutralLevel) && (spaceThrust.kineticCCW < p.kineticNeutralLevel) ) {
    spaceThrust.kineticCCW = 0;
   }


  //Compute space thrust
  spaceThrust.CW = spaceThrust.kineticCW / (p.kineticMaxLevel / 100);
  spaceThrust.CCW = spaceThrust.kineticCCW / (p.kineticMaxLevel / 100);
  
  return spaceThrust;
}

//Apply max limit value on thruster
//Usefull when a thuster is less effective
//in one direction than other (reverse/forward)
struct thrustLevel applyMaxLimits (struct thrustLevel thrust, int forwardMaxThrust, int reverseMaxThrust){
   //Do we exceed max authorized power?
   //If so, need to make proportionnal value and cap it
   //For CW motor
   if( (thrust.CW > 0) && (thrust.CW > forwardMaxThrust) ){
     thrust.CW = thrust.CW * (forwardMaxThrust / 100.0);
   } else  if( (thrust.CW < 0) && (thrust.CW < -reverseMaxThrust) ){
     thrust.CW = thrust.CW * (reverseMaxThrust / 100.0);
   }
   //For CCW motor
   if( (thrust.CCW > 0) && (thrust.CCW > forwardMaxThrust) ){
     thrust.CCW = thrust.CCW * (forwardMaxThrust / 100.0);
   } else  if( (thrust.CCW < 0) && (thrust.CCW < -reverseMaxThrust) ){
     thrust.CCW = thrust.CCW * (reverseMaxThrust / 100.0);
   }

   return thrust;
}

//Apply thrust values to thruster
//Use ESC (aka servo) to drive triphase engine
void driveThrusters (struct thrustLevel thrustX, struct thrustLevel thrustY, struct thrustLevel thrustZ){
  //We have ARMED thrusters
  if (armed == true){
    xCW.writeMicroseconds(map(thrustX.CW,-100, 100, 1000, 2000));
    xCCW.writeMicroseconds(map(thrustX.CCW,-100, 100, 1000, 2000));
    yCW.writeMicroseconds(map(thrustY.CW,-100, 100, 1000, 2000));
    yCCW.writeMicroseconds(map(thrustY.CCW,-100, 100, 1000, 2000));
    zCW.writeMicroseconds(map(thrustZ.CW,-100, 100, 1000, 2000));
    zCCW.writeMicroseconds(map(thrustZ.CCW,-100, 100, 1000, 2000));
  } else {
    //Let's disarm thrusters
    //Full OFF on every axis
    xCW.writeMicroseconds(1500);
    xCCW.writeMicroseconds(1500);
    yCW.writeMicroseconds(1500);
    yCCW.writeMicroseconds(1500);
    zCW.writeMicroseconds(1500);
    zCCW.writeMicroseconds(1500);
  }
}
  
//debug function
//all structs are declared wide.
void printValues (){

  Serial.print("translate X=");
  Serial.print(translation.X);
  Serial.print(" Y=");
  Serial.print(translation.Y);
  Serial.print(" Z=");
  Serial.print(translation.Z);
  
  Serial.print("    rotate X=");
  Serial.print(rotation.X);
  Serial.print(" Y=");
  Serial.print(rotation.Y);
  Serial.print(" Z=");
  Serial.println(rotation.Z);


  //Per thruster power value
  Serial.print("Thruster power X(CW:");
  Serial.print(thrustX.CW);
  Serial.print(" CCW:");
  Serial.print(thrustX.CCW);
  Serial.print(" Kinetic CW:");
  Serial.print(thrustX.kineticCW);
  Serial.print(" CCW:");
  Serial.print(thrustX.kineticCCW);
  Serial.print(") Y(CW:");
  Serial.print(thrustY.CW);
  Serial.print(" CCW:");
  Serial.print(thrustY.CCW);
  Serial.print(" Kinetic CW:");
  Serial.print(thrustY.kineticCW);
  Serial.print(" CCW:");
  Serial.print(thrustY.kineticCCW);
  Serial.print(") Z(CW:");
  Serial.print(thrustZ.CW);
  Serial.print(" CCW:");
  Serial.print(thrustZ.CCW);
  Serial.print(" Kinetic CW:");
  Serial.print(thrustZ.kineticCW);
  Serial.print(" CCW:");
  Serial.print(thrustZ.kineticCCW);
  Serial.println(")");
}

//debug function
//all structs are declared wide.
void printParameters (){
  //Debug
  Serial.print("Debug =");
  Serial.println(p.debug);

  //Space mode
  Serial.print("Space mode =");
  Serial.println(p.spaceMode);
  
  //Translate
  Serial.print("Inversed Translate X=");
  Serial.println(p.inverseTranslateX);
  Serial.print("Inversed Translate Y=");
  Serial.println(p.inverseTranslateY);
  Serial.print("Inversed Translate Z=");
  Serial.println(p.inverseTranslateZ);

  //Rotate
  Serial.print("Inversed Rotate X=");
  Serial.println(p.inverseRotateX);
  Serial.print("Inversed Rotate Y=");
  Serial.println(p.inverseRotateY);
  Serial.print("Inversed Rotate Z=");
  Serial.println(p.inverseRotateZ);
    
  //Neutral percent
  Serial.print("Neutral ignore%=");
  Serial.println(p.neutralPercent);

  //Kinetic neutral level
  Serial.print("Kinetic neutral ignore%=");
  Serial.println(p.kineticNeutralLevel);

  //Kinetic max level
  Serial.print("Kinetic max level=");
  Serial.println(p.kineticMaxLevel);

  //Thruster max level
  Serial.print("Thruster X FW max%=");
  Serial.println(p.thrusterXForwardMax);
  Serial.print("Thruster X RV max%=");
  Serial.println(p.thrusterXReverseMax); 
     
  Serial.print("Thruster Y FW max%=");
  Serial.println(p.thrusterYForwardMax);
  Serial.print("Thruster Y RV max%=");
  Serial.println(p.thrusterYReverseMax);   
  
  Serial.print("Thruster Z FW max%=");
  Serial.println(p.thrusterZForwardMax);
  Serial.print("Thruster Z RV max%=");
  Serial.println(p.thrusterZReverseMax);   
}


//Load Eeprom content in parameters
void loadEEPROM() {

  // Read eeprom
  EEPROM.get(0, p);

  Serial.println("Reading eeprom");
  
  // No custom data saved
  //Imput default values
  if (p.magic != STRUCT_MAGIC) {
    Serial.println("Empty Eeprom, applying default values");
    //First clear Eeprom
    //for (int i = 0 ; i < EEPROM.length() ; i++) {
    //  EEPROM.write(i, 0);
    //}
    p.inverseTranslateX=false;
    p.inverseTranslateY=false;
    p.inverseTranslateZ=false;
    p.inverseRotateX=false;
    p.inverseRotateY=false;
    p.inverseRotateZ=false;
    p.neutralPercent=8;
    p.spaceMode=false;
    p.kineticNeutralLevel=10;
    p.kineticMaxLevel=1000;
    p.thrusterXForwardMax=75;
    p.thrusterXReverseMax=100;
    p.thrusterYForwardMax=75;
    p.thrusterYReverseMax=100;
    p.thrusterZForwardMax=75;
    p.thrusterZReverseMax=100;
    p.debug=false;

    // Backup data
    saveEEPROM();
    //Proint default values
    printParameters();
  } 

  //Debug values
  if(p.debug==true) printParameters();
}

//Save parameters to eeprom
void saveEEPROM() {
  p.magic = STRUCT_MAGIC;
  p.struct_version =  STRUCT_VERSION;
  EEPROM.put(0, p);
}



void recvWithStartEndMarkers() {
    static boolean recvInProgress = false;
    static byte ndx = 0;
    char startMarker = '$';
    char endMarker = '!';
    char rc;

    while (Serial1.available() > 0 && newData == false) {
        rc = Serial1.read();

        if (recvInProgress == true) {
            if (rc != endMarker) {
                receivedChars[ndx] = rc;
                ndx++;
                if (ndx >= numChars) {
                    ndx = numChars - 1;
                }
            }
            else {
                receivedChars[ndx] = '\0'; // terminate the string
                recvInProgress = false;
                ndx = 0;
                newData = true;
            }
        }

        else if (rc == startMarker) {
            recvInProgress = true;
        }
    }
}
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
void loop() {

  //MISSING
  //SpaceMode button switch
  //Armed/Disarmed switch
  //Status light
  
  // read joystock position:
  translateX = analogRead(translateXpin);
  translateY = analogRead(translateYpin);
  translateZ = analogRead(translateZpin);
  
  rotateX = analogRead(rotateXpin);
  rotateY = analogRead(rotateYpin);
  rotateZ = analogRead(rotateZpin);
  
  //Convert raw joystick values to percent
  //For translation
  translation.X = joystickToPercent(translateX, p.inverseTranslateX);
  translation.Y = joystickToPercent(translateY, p.inverseTranslateY);
  translation.Z = joystickToPercent(translateZ, p.inverseTranslateZ);

  //For rotation
  rotation.X = joystickToPercent(rotateX, p.inverseRotateX);
  rotation.Y = joystickToPercent(rotateY, p.inverseRotateY);
  rotation.Z = joystickToPercent(rotateZ, p.inverseRotateZ);

  //Read serial link for any orders
  recvWithStartEndMarkers();
    if (newData == true) {
        strcpy(tempChars, receivedChars);
        // this temporary copy is necessary to protect the original data
        //   because strtok() used in parseData() replaces the commas with \0
        parseData();
        newData = false;
    }

  //Convert PercentJoystick to real thrust
  thrustX = percentToThrust(thrustX, translation.X, rotation.X);
  thrustY = percentToThrust(thrustY, translation.Y, rotation.Y);
  thrustZ = percentToThrust(thrustZ, translation.Z, rotation.Z);

  //Space mode. Each action needs to be reciproced
  if ( p.spaceMode == true ){
    thrustX = spaceKineticThrust(thrustX);
    thrustY = spaceKineticThrust(thrustY);
    thrustZ = spaceKineticThrust(thrustZ);
  }

  //Check and apply max limit power
  thrustX = applyMaxLimits(thrustX, p.thrusterXForwardMax, p.thrusterXReverseMax);
  thrustY = applyMaxLimits(thrustY, p.thrusterYForwardMax, p.thrusterYReverseMax);
  thrustZ = applyMaxLimits(thrustZ, p.thrusterZForwardMax, p.thrusterZReverseMax);

  //Drive thruster (only if armed)<, within function
  driveThrusters(thrustX, thrustY, thrustZ);
  
  //Debug print
  if(p.debug==true) printValues();


  delay(250);
  

}

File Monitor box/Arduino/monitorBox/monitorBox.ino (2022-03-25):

#include "Adafruit_GFX.h"
#include "Adafruit_ILI9341.h"
#include <XPT2046_Touchscreen.h>
#include <SPI.h>

#define TFT_DC 40
#define TFT_CS 41
//software SPI for TFT
#define TFT_MOSI 42
#define TFT_CLK 43
#define TFT_MISO 44

#define CS_PIN 44

#define TS_MINX 300
#define TS_MINY 300
#define TS_MAXX 3900
#define TS_MAXY 3900

#define DIVE true
#define SPACE false

#define XPLUST 1
#define XMINT 2
#define YPLUST 3
#define YMINT 4
#define ZPLUST 5
#define ZMINT 6
#define XPLUSR 7
#define XMINR 8
#define YPLUSR 9
#define YMINR 10
#define ZPLUSR 11
#define ZMINR 12

//hardware SPI for TS
//#define TFT_MOSI 51
//#define TFT_CLK 52
//#define TFT_MISO 50

XPT2046_Touchscreen ts(CS_PIN);

//XPT2046_Touchscreen ts(CS_PIN);  // Param 2 - NULL - No interrupts
//XPT2046_Touchscreen ts(CS_PIN, 255);  // Param 2 - 255 - No interrupts
//XPT2046_Touchscreen ts(CS_PIN, TIRQ_PIN);  // Param 2 - Touch IRQ Pin - interrupt enabled polling

Adafruit_ILI9341 tft = Adafruit_ILI9341(TFT_CS, TFT_DC, TFT_MOSI, TFT_CLK);

bool armed=false;
bool mode=DIVE;
short axis=0;
short speed=0;
short oldSpeed=0;

void setup() {
  
  Serial.begin(115200);
  Serial1.begin(115200);
  tft.begin(16000000);
  tft.setRotation(1);
  tft.fillScreen(ILI9341_NAVY);
  ts.begin();
  //ts.setRotation(1);
  while (!Serial && (millis() <= 1000));
  drawMenu();

  
}

boolean wastouched = true;

void loop() {
  int x, y;

  boolean istouched = ts.touched();
  if (istouched) {
    TS_Point p = ts.getPoint();
    //Convert to real x,y coordinate
    //x = map(p.x,300,3900,0,320);
    //y = map(p.y,300,3900,0,240);
    x = map(p.x, TS_MINX, TS_MAXX, 0, tft.width());
    y = map(p.y, TS_MINY, TS_MAXY, 0, tft.height());


/*
    //Map armed function
    if((x >= 178)&&(x<=318)&&(y>=3)&&(y<=46)){
      if (armed == true) armed = false; else armed = true;
      drawArmed(armed);
    }
    //Map dive/space mode
    if((x >= 3)&&(x<=146)&&(y>=3)&&(y<=46)){
      if (mode == DIVE) mode = SPACE; else mode = DIVE;
      drawMode(mode);
    }
    */
    //Map dive/space mode
    if((x >= 1)&&(x<=74)&&(y>=1)&&(y<=36)){
      if (mode == DIVE) mode = SPACE; else mode = DIVE;
      drawMode(mode);
    }
    //Map armed function
    if((x >= 1)&&(x<=74)&&(y>=38)&&(y<=75)){
      if (armed == true) armed = false; else armed = true;
      drawArmed(armed);
    }
    //Map speed 
    for(int i=1;i<=9;i++){
      if((x >= (27*i)+50)&&(x<=(27*i)+77)&&(y>=12)&&(y<=62)){
        if(speed != i)oldSpeed=speed;
        drawSpeed(i,true);
        speed=i;
      }
    }
    //Translation
    //map X+ T
    if((x >= 107)&&(x<=157)&&(y>=158)&&(y<=238)){
      axis = XPLUST; 
      drawPadElement('X', true, 'T', 1);
    }
    //map X- T
    if((x >= 3)&&(x<=53)&&(y>=158)&&(y<=238)){
      axis = XMINT; 
      drawPadElement('X', false, 'T', 1);
    }
    //map Y+ T
    if((x >= 55)&&(x<=105)&&(y>=76)&&(y<=156)){
      axis = YPLUST; 
      drawPadElement('Y', true, 'T', 1);
    }
    //map Y- T
    if((x >= 55)&&(x<=105)&&(y>=158)&&(y<=238)){
      axis = YMINT; 
      drawPadElement('Y', false, 'T', 1);
    }
    //map Z+ T
    if((x >= 3)&&(x<=53)&&(y>=76)&&(y<=156)){
      axis = ZPLUST; 
      drawPadElement('Z', true, 'T', 1);
    }
    //map Z- T
    if((x >= 107)&&(x<=157)&&(y>=76)&&(y<=156)){
      axis = ZMINT; 
      drawPadElement('Z', false, 'T', 1);
    }
    //Rotation
    //map X+ R
    if((x >= 107+160)&&(x<=157+160)&&(y>=158)&&(y<=238)){
      axis = XPLUSR; 
      drawPadElement('X', true, 'R', 1);
    }
    //map X- R
    if((x >= 3+160)&&(x<=53+160)&&(y>=158)&&(y<=238)){
      axis = XMINR; 
      drawPadElement('X', false, 'R', 1);
    }
    //map Y+ R
    if((x >= 55+160)&&(x<=105+160)&&(y>=76)&&(y<=156)){
      axis = YPLUSR; 
      drawPadElement('Y', true, 'R', 1);
    }
    //map Y- R
    if((x >= 55+160)&&(x<=105+160)&&(y>=158)&&(y<=238)){
      axis = YMINR; 
      drawPadElement('Y', false, 'R', 1);
    }
    //map Z+ R
    if((x >= 3+160)&&(x<=53+160)&&(y>=76)&&(y<=156)){
      axis = ZPLUSR; 
      drawPadElement('Z', true, 'R', 1);
    }
    //map Z- R
    if((x >= 107+160)&&(x<=157+160)&&(y>=76)&&(y<=156)){
      axis = ZMINR; 
      drawPadElement('Z', false, 'R', 1);
    }
  } else {
      switch(axis){
        case XPLUST:
          drawPadElement('X', true, 'T', 0);
          break;
        case XMINT:
          drawPadElement('X', false, 'T', 0);
          break;
        case YPLUST:
          drawPadElement('Y', true, 'T', 0);
          break;
        case YMINT:
          drawPadElement('Y', false, 'T', 0);
          break;
        case ZPLUST:
          drawPadElement('Z', true, 'T', 0);
          break;
        case ZMINT:
          drawPadElement('Z', false, 'T', 0);
          break;
        case XPLUSR:
          drawPadElement('X', true, 'R', 0);
          break;
        case XMINR:
          drawPadElement('X', false, 'R', 0);
          break;
        case YPLUSR:
          drawPadElement('Y', true, 'R', 0);
          break;
        case YMINR:
          drawPadElement('Y', false, 'R', 0);
          break;
        case ZPLUSR:
          drawPadElement('Z', true, 'R', 0);
          break;
        case ZMINR:
          drawPadElement('Z', false, 'R', 0);
          break;
      }
      axis=0;
      //Refresh speed if needed
      if(oldSpeed != 0){
        drawSpeed(oldSpeed,false);
        oldSpeed = 0;
      }
  }
  //Recopy any serial info
  if (Serial.available() > 0) {
    Serial1.write(Serial.read());
  }
  /*
   * Should not be used, as we are only in master mode
  if (Serial1.available() > 0) {
    Serial.write(Serial1.read());
  }
  */
  //delay(50);
}


/*
void drawArmed(bool enable){
  if(enable){
    Serial.println("Armed");
    //Armed
    tft.drawRoundRect(178,3,140, 43, 4, ILI9341_WHITE);
    tft.fillRoundRect(178,3,140, 43, 4, ILI9341_RED);
    tft.setCursor(205,14);
    tft.setTextColor(ILI9341_WHITE, ILI9341_RED);
    tft.setTextSize(3);
    tft.print("ARMED");
  }else {
    Serial.println("Disarmed");
    //Disarmed
    tft.drawRoundRect(178,3,140, 43, 4, ILI9341_WHITE);
    tft.fillRoundRect(178,3,140, 43, 4, ILI9341_GREEN); 
    tft.setCursor(203,18);
    tft.setTextColor(ILI9341_BLACK, ILI9341_GREEN);
    tft.setTextSize(2);
    tft.print("DISARMED");
  }
}

void drawMode(bool mode){
  if(mode == DIVE){
    //Currently in Dive mode
    tft.drawRoundRect(3,3,140, 43, 4, ILI9341_WHITE);
    tft.fillRoundRect(3,3,140, 43, 4, ILI9341_BLUE);
    tft.setCursor(38,15);
    tft.setTextColor(ILI9341_WHITE, ILI9341_BLUE);
    tft.setTextSize(3);
    tft.print("DIVE");
  }else{
    //Currently in Space mode
    tft.drawRoundRect(3,3,140, 43, 4, ILI9341_WHITE);
    tft.fillRoundRect(3,3,140, 43, 4, ILI9341_LIGHTGREY);
    tft.setCursor(31,15);
    tft.setTextColor(ILI9341_WHITE, ILI9341_LIGHTGREY);
    tft.setTextSize(3);
    tft.print("SPACE");
  }
}
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
